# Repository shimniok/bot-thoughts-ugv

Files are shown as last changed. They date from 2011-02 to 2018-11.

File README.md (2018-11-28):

This is the repository of electronics and software for Data Bus and Troubled Child, my autonomous ground vehicles. 

* [Troubled Child](http://www.bot-thoughts.com/2014/06/avc-sharc-fsv.html) is a 1986 Jeep Grand Wagoneer that took 1st place in the 2014 Sparkfun AVC.
* [Data Bus](http://www.bot-thoughts.com/p/robot-mag-data-bus.html) is a 1:10 scale RC car that took 3rd place in the 2012 Sparkfun AVC.

The repository contains source code, schematics, board layouts, and documentation. Mostly this is a catch-all for what I worked on in 2010-2014.

* [Current Software](https://github.com/shimniok/diyrovers) - updated versions of the mbed software that handles pose estimation, navigation, and path following
* ```Software/``` - *older* mbed software that handles pose estimation, navigation, path following
* ```Documentation/``` - various supporting documents
* ```Hardware/``` - various hardware used in building and calibrating
* ```Electronics/``` - catch-all of circuit/layout designs varying from experiment to tried and tossed

Some of the electronics are now products on [Tindie.com](https://www.tindie.com/stores/bot_thoughts/) and they have their own repositories, shown below.

# Rover Products
* [RoverMux](https://github.com/shimniok/RoverMux) tried and true 3 channel R/C Multiplexer
* [RoverBaseboard](https://github.com/shimniok/RoverBaseboard) - a baseboard making it easy to hook up servos and sensors to an mbed/LPCXpresso
* [RoverGyro](https://github.com/shimniok/RoverGyro) - a breakout for low drift MAX21000 gyro (untested)
* [RoverPower](https://github.com/shimniok/RoverPower) - high current 5V power supply (untested)
* [RoverMeter](https://github.com/shimniok/RoverMeter) - I2C-based current monitor (untested)

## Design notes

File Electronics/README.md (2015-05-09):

# Circuits for Sparkfun AVC Robot 2011

Various circuits for 2011 AVC ground robot

* 5vadcmbed/ - 5V-capable ADC for mbed
* Block Diagram.sch - block diagram for data bus
* cmucambridge/ - serial to I2C bridge for CMUcam (incomplete)
* duplexoptoiso/ - full duplex opto isolator, used during GPS experiments
* gfxlcd/ - graphic LCD
* microsdbreakout/ - maybe an old version of [eeZeeMicroSD](https://github.com/shimniok/eeZeeMicroSD)
* motherboard/ - original verion(s) of [RoverBaseboard](https://github.com/shimniok/RoverBaseboard)
* pdmodule/ - simple power distribution module 
* powersupply/ - power supply for MCU
* powersupply5/ - power supply for MCU
* rangeri2c/ - early version of analog-to-I2C module?
* rckillswitch/ - early version of [RoverMux](https://github.com/shimniok/RoverMux)
* seriali2cbridge/ - serial to I2C bridge, probably for AVRcam
* venusgps/ - Venus GPS mounting board(?)
* warningflasher/ - a warning flasher letting people know the vehicle is in autonomous mode
* wheelencoderadapter/ - an early version of [RoverEncoder](https://github.com/shimniok/RoverEncoder)

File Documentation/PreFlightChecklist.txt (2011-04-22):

=====================================================
================ Pre-Event Checklist ================ 
=====================================================

[ ] Correct config used, waypoints, declination to SFE site
[ ] All stuff packed (see PitKit.txt checklist)
[ ] Tool kit inventory, load in vehicle

=====================================================
================ Pre-Flight Checklist =============== 
=====================================================

[ ] Wheels mounted tightly

[ ] Battery connected and charged

[ ] Start button plugged in

[ ] Obj detection plugged in

[ ] Compass connected

[ ] GPS connected

[ ] Body clips on

[ ] Obj detection mounted

[ ] Compass/GPS mounted, aligned

[ ] AHRS mounted and connected

[ ] SD Card installed

=====================================================
==================== Staging Area =================== 
=====================================================

[ ] Camera powered on

[ ] MCU powered on

[ ] Wheel encoders working, not skipping

[ ] Motor power connected

[ ] Remote control is OFF

[ ] ESC powered up, operational

[ ] AHRS functional

[ ] File logging functioning

[ ] GPS fix established

=====================================================
=============== Post-Fight Checklist ================ 
=====================================================

[ ] charge battery

[ ] remove data log and plot

[ ] download camera data

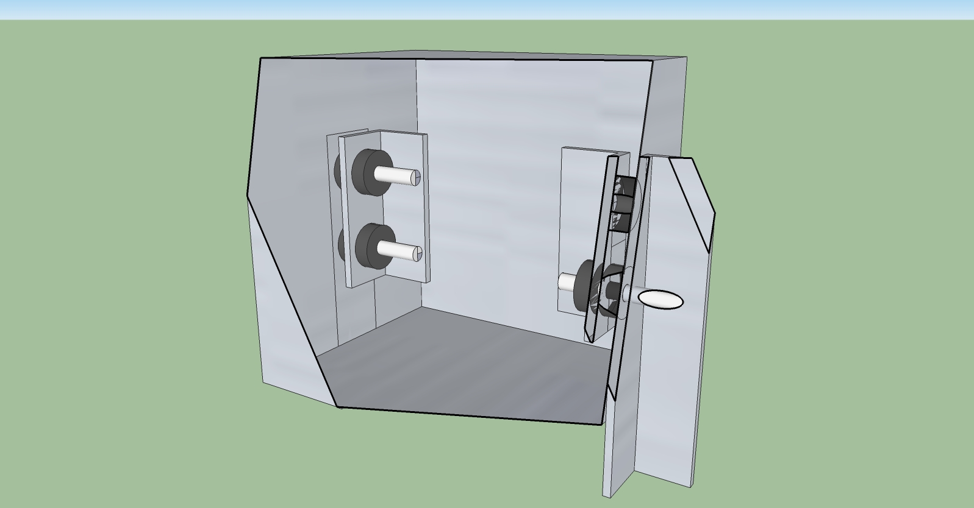
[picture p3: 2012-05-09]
Hardware/AVRcamMount.jpg

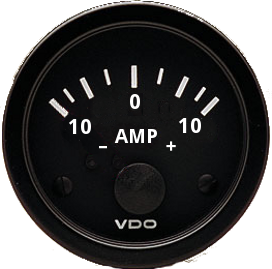
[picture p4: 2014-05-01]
Software/GCS/BotThoughtsGCS/src/com/botthoughts/gcs/resources/ammeter3.png

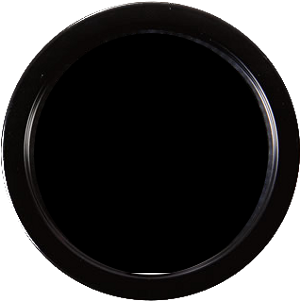
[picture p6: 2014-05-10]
Software/GCS/BotThoughtsGCS/src/com/botthoughts/gcs/resources/compass.png

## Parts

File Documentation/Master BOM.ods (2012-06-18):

Bot Thoughts UGV “Data Bus” for 2012 Sparkfun AVC |  |  |  |  | Key
As complete as I can make it; I'm sure I'm forgetting some things. |  |  |  |  | used it | didn't use it | inaccurate
Master BOM
Item | Description | Supplier | Manufacturer | Part Number | Cost | Qty | Total | Changes
RC Car Chassis
R/C Car | ElectrixRC Circuit 1/10 RC Stadium Truck | RC Hobbies | ElectrixRC | n/a | $140.00 | 1 | $140.00
Battery | 4000mAH 25C ROAR battery | Hobbypartz | Gens Ace | 98P-25C-2400-2S1P-HardCase | $20.00 | 1 | $20.00
Tires | Traxxas Anaconda on All Star black chrome (pair) | RC Hobbies | Traxxas | 3776A | $25.99 | 2 | $51.98
Springs | ElectrixRC Springs, Stiff | A Main Hobbies | ECX | ECX1080 | $6.39 | 1 | $6.39
Shock oil | Losi 50wt shock oil | Hobbytown USA | Losi | LOSA5227 | $4.00 | 1 | $4.00 | 2012
ESC | Hobbywing eZrun 35A ESC | Hobbypartz | HobbyWing | 07E-eZRun-35A-SL-ESC | $29.64 | 1 | $29.64 | 2012
Motor | Tacon 3000Kv 3660-540L-8T | Hobbypartz | Tacon | 96M213-3660-3000KV-8T | $32.20 | 1 | $32.20 | 2012
Body | Skool Bus lexan body | Tower Hobbies | Parma | LXEER5 | $23.99 | 1 | $23.99
Paint | RC Body paint (3 colors) | RC Hobbies | Pactra / Testors | various | $6.29 | 3 | $18.87
Body clips | RC 1:10 body clips | A Main Hobbies | ECX | ECX1048 | $1.89 | 1 | $1.89
Body posts | 2 pair, HPI body posts | RC Hobbies | HPI | #6507 | $5.59 | 2 | $11.18
Lexan sheet | Lexan sheet, .093”x8”x10” electronics platform, bumper | Home Depot | SABIC Innovative Plastics | n/a | $3.98 | 1 | $3.98 | 2012
Brass strip | Brass strip, 2” x 12” x 0.032” | Big Tool Box | K&S | n/a | $3.79 | 1 | $3.79
Brass strip | Brass strip, 1” x 12” x 0.032” | Big Tool Box | K&S | n/a | $2.29 | 1 | $2.29
Aluminum strip | Front skid plate/bumper mount | Big Tool Box |  |  |  | 1 | $0.00 | 2012
Sheet aluminum | Front skid plate/bumper mount | Big Tool Box |  |  |  | 1 | $0.00 | 2012
Aluminum L | Cow catcher / bumper | Big Tool Box |  |  |  | 1 | $0.00 | 2012
Aluminum L | Electronics platform mounting | Big Tool Box |  |  |  | 1 | $0.00 | 2012
Aluminum L | Electronics platform mounting | Big Tool Box |  |  |  | 1 | $0.00 | 2012
Nylon PCB spacers | Spacers for Lexan platform, 0.375”, chassis front | All Electronics | unknown | SP-228 | $0.05 | 2 | $0.10
Aluminum rivets | Rivets for mounting brackets | self | parts bin | n/a | $0.00 | 2 | $0.00 | 2012
#10 Nylon Spacers | Spacers for motherboard mounting | self | parts bin | n/a | $0.00 | 4 | $0.00 | 2012
#10 nylock nuts | Nuts for electronics platform | self | parts bin | n/a | $0.00 | 4 | $0.00 | 2012
#10 x 1.5” machine screw | Bolts for electronics platform | self | parts bin | n/a | $0.00 | 4 | $0.00 | 2012
Deans connectors | Deans battery connectors | A Main Hobbies | Deans | WSD1300 | $2.99 | 2 | $5.98 | 2012
Microcontroller and Motherboard
Microcontroller | NXP mbed LPC1768 ARM Cortex M3 microcontroller | Sparkfun | NXP | DEV-09564 | $59.95 | 1 | $59.95
microSD socket | microSD slot | Sparkfun | Amphenol | PRT-00127 | $3.95 | 1 | $3.95 | 2012
microSD card | microSD card, 2G | Microcenter | unknown | unknown | $12.99 | 1 | $12.99 | 2012
LCD Display | Serial Graphic LCD | Sparkfun | Sparkfun | LCD-09351 | $34.95 | 1 | $34.95 | 2012
Interface buttons | SPST Normally Open Pushbutton Momentary Switch | Radio Shack | Radio Shack | 275-646, 275-644 | $2.99 | 3 | $8.97 | 2012
Sensors
GPS | Venus638FLPX SMA breakout board | Sparkfun | SkyTraq | GPS-11058 | $49.95 | 1 | $49.95 | 2012
GPS Ground plane | Tin sheet | Big Tool Box | K&S |  |  |  | $0.00 | 2012
IR Rangers | Sharp GP2Y0A02YK0F 150cm IR Ranger | Sparkfun | Sharp | SEN-08958 | $14.95 | 1 | $14.95 | 2012
IMU | Pololu MinIMU-9 | Pololu | Pololu | #1265 | $49.95 | 1 | $49.95 | 2012
Encoder sensors | QRE1113 analog breakout board | Sparkfun | Sparkfun | ROB-09453 | $2.95 | 1 | $2.95 | 2012
Encoder boards | Schmitt-trigger comparator interface board | Bot Thoughts | Bot Thoughts | n/a | $6.00 | 1 | $6.00 | 2012
RC Switch Board
74HC244 | Bus Driver / Switch | Newark | STMicro | 18C7559 | $0.57 | 1 | $0.57
LM258 | Operational Amplifier | Newark | STMicro | 89K0661 | $0.23 | 1 | $0.23
Power supply
LDO Regulator | 3A switching step-down regulator | Pololu | Pololu | D15V35F5S3 | $14.95 | 1 | $14.95
Misc Electronic Components
PCB | Printed circuit board, 1oz copper, 6” square | Digikey | MG Chemicals | 473-1006-ND | $7.24 | 1 | $7.24 | 2012
#2 nuts | Nuts for custom PCB mounting | Radio Shack |  |  | $1.99 | 1 | $1.99 | 2012
#2 standoffs | PCB standoffs | unknown | unknown |  | $0.00 | 0 | $0.00 | 2012
#2 bolts | Bolts for custom PCB mounting | Radio Shack |  |  | $1.99 | 1 | $1.99 | 2012
#4 nuts | Nuts for custom PCB mounting | Radio Shack |  |  | $1.99 | 1 | $1.99 | 2012
#4 standoffs | PCB standoffs, 100pk | Smallparts.com | unknown |  | $6.56 | 0.16 | $1.05 | 2012
#f bolts | Bolts for custom PCB mounting | Radio Shack |  |  | $1.99 | 1 | $1.99 | 2012
double sided tape | Double sided tape for sensor mounting | Hobby Lobby | Scotch 3M |  | $4.55 | 1 | $4.55 | 2012
 |  |  |  |  |  |  | $637.44 | TOTAL

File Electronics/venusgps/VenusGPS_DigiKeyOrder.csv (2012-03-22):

Digi-Key Part Number | Manufacturer Name | Manufacturer Part Number | Customer Reference | Quantity 1 | Quantity 2 | Quantity 3
3000K-ND | Keystone | 3000 | ? | 1 | ? | ?

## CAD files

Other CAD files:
Hardware/AVRcamMount.skp
Hardware/turntable.skp
Hardware/turntable_exploded.skp

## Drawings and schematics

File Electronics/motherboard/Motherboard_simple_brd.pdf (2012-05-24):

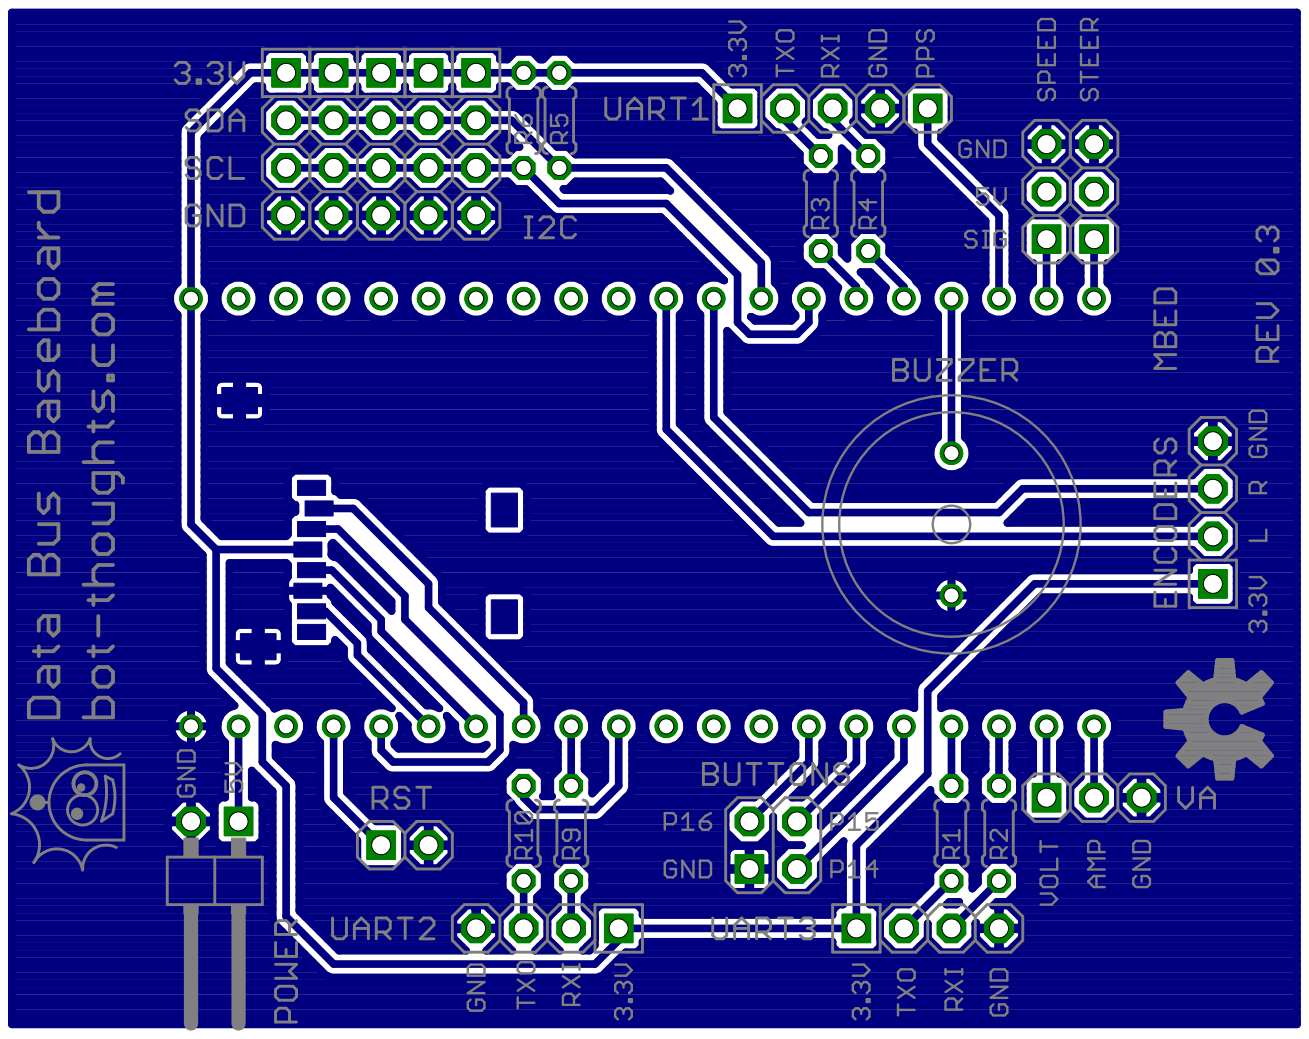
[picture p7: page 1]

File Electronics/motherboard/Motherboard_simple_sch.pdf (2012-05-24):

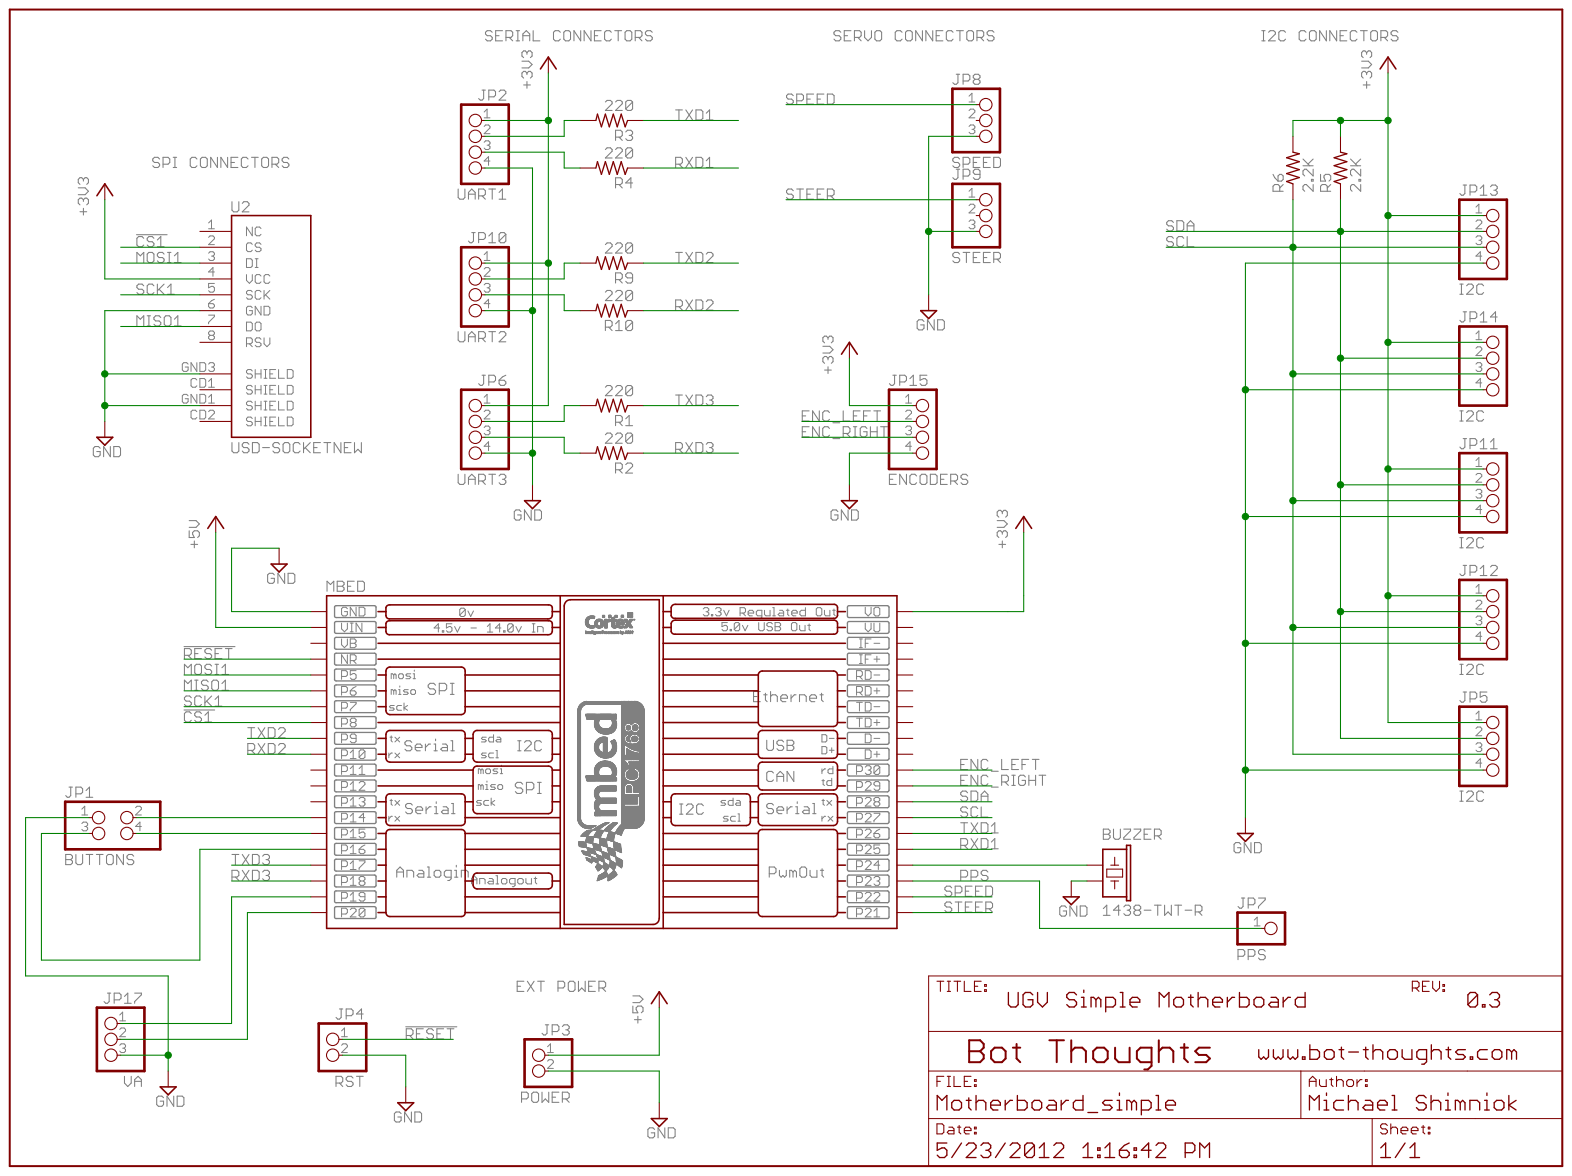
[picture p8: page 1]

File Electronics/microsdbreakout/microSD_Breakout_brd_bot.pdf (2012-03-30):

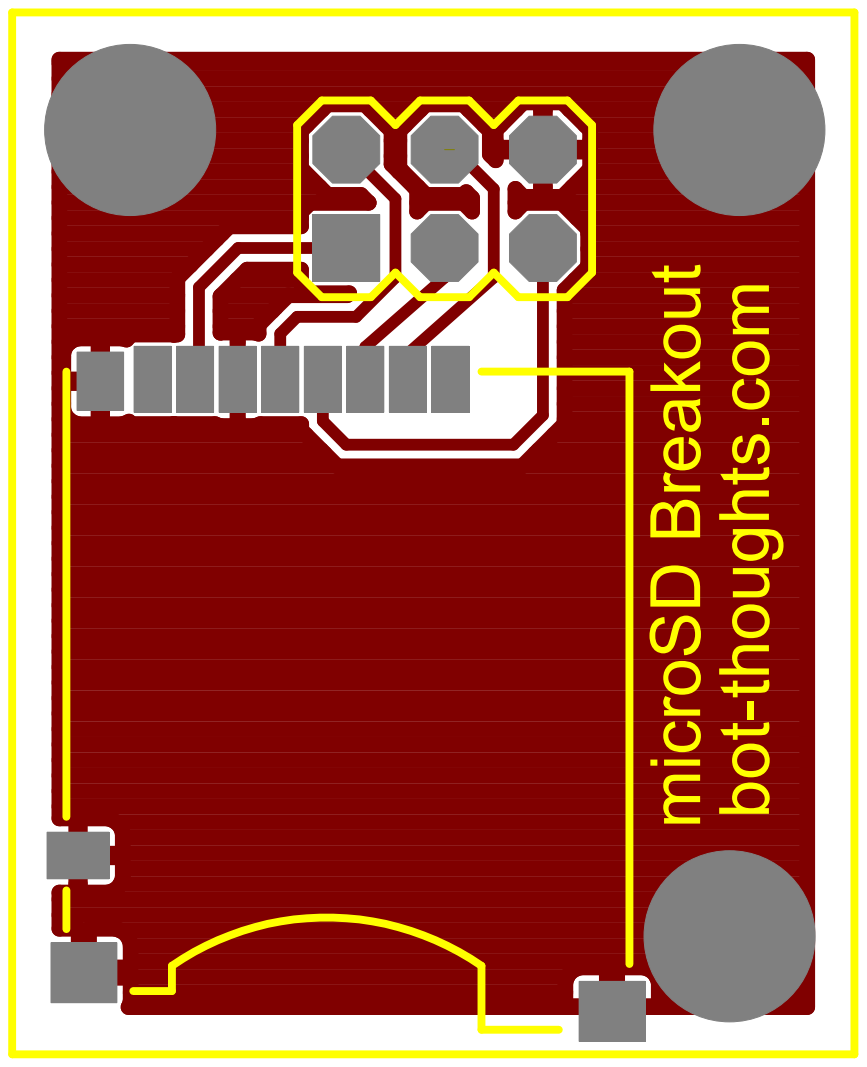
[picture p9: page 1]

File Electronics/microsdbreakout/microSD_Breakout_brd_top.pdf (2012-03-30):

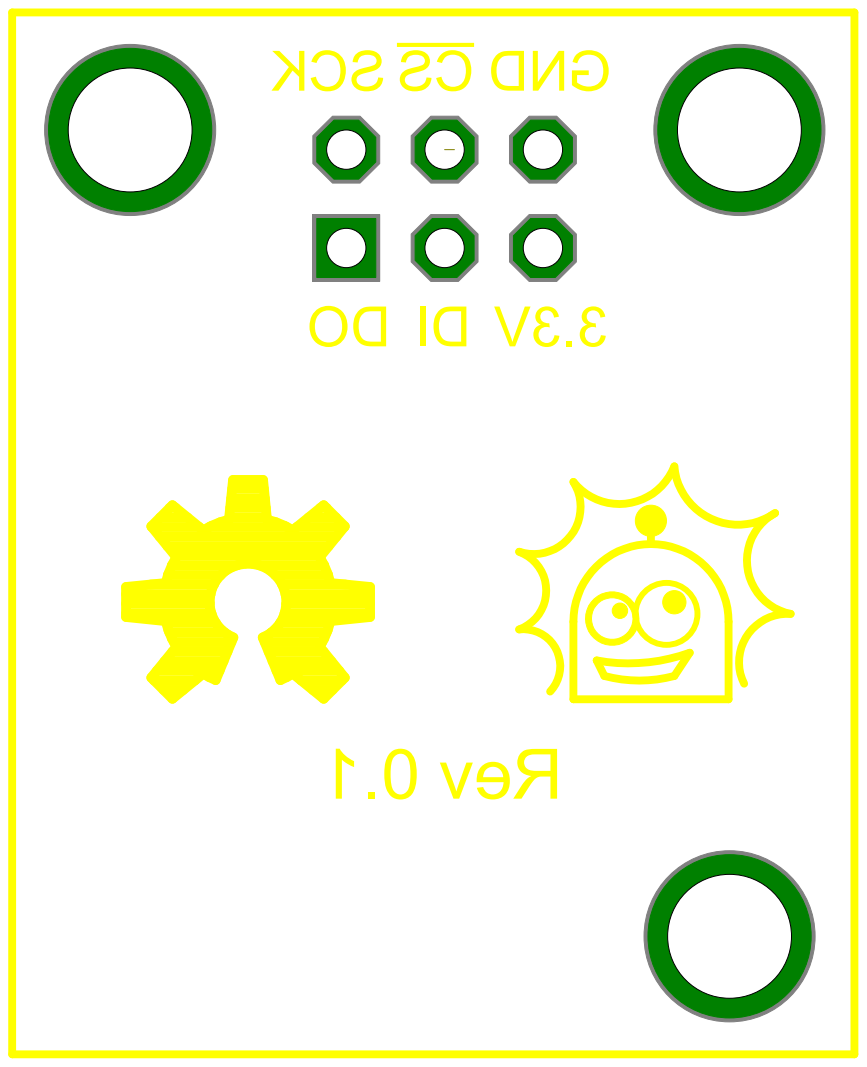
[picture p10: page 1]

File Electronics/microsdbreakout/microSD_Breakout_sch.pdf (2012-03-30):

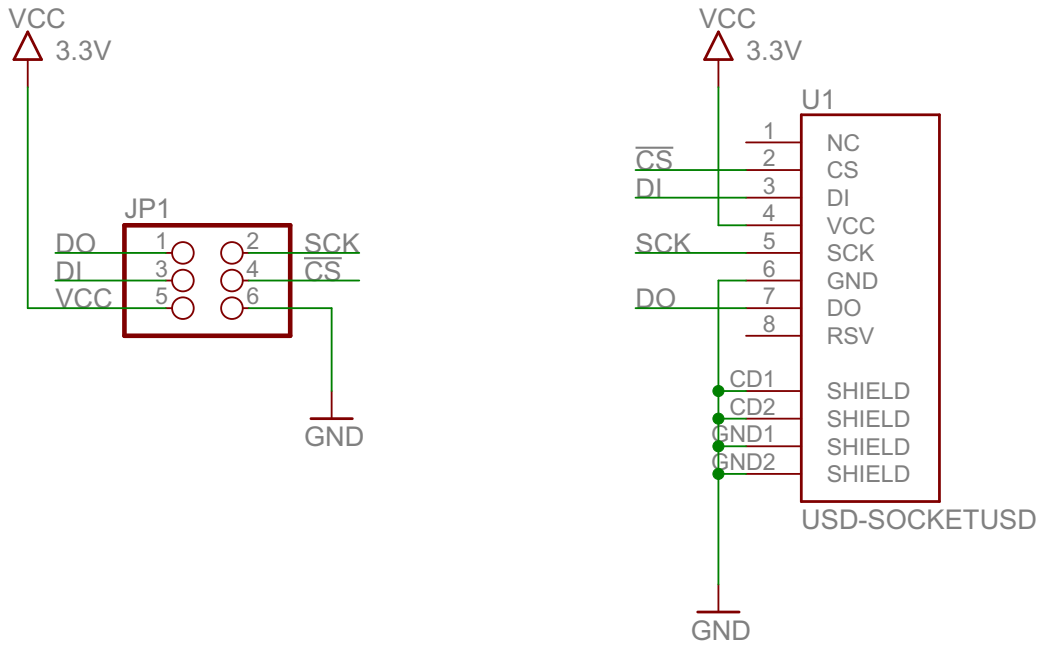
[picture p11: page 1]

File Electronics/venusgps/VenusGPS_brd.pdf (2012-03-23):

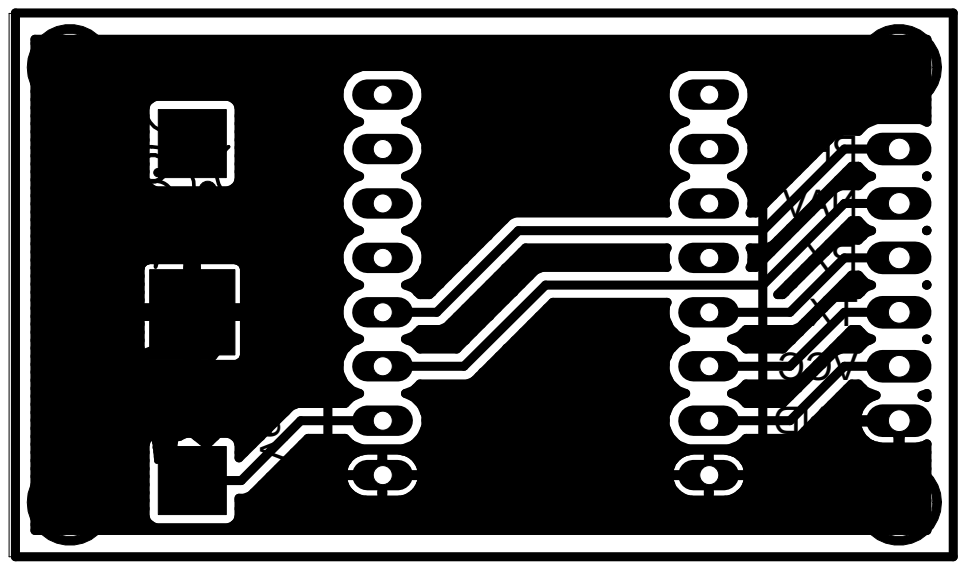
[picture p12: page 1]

bot-thoughts.com XT CCV DNGXR SPP VAN Venus GPS Interface 1. 0 veR

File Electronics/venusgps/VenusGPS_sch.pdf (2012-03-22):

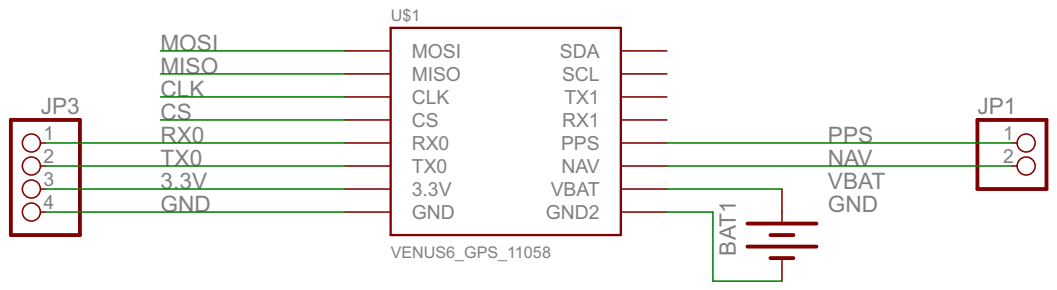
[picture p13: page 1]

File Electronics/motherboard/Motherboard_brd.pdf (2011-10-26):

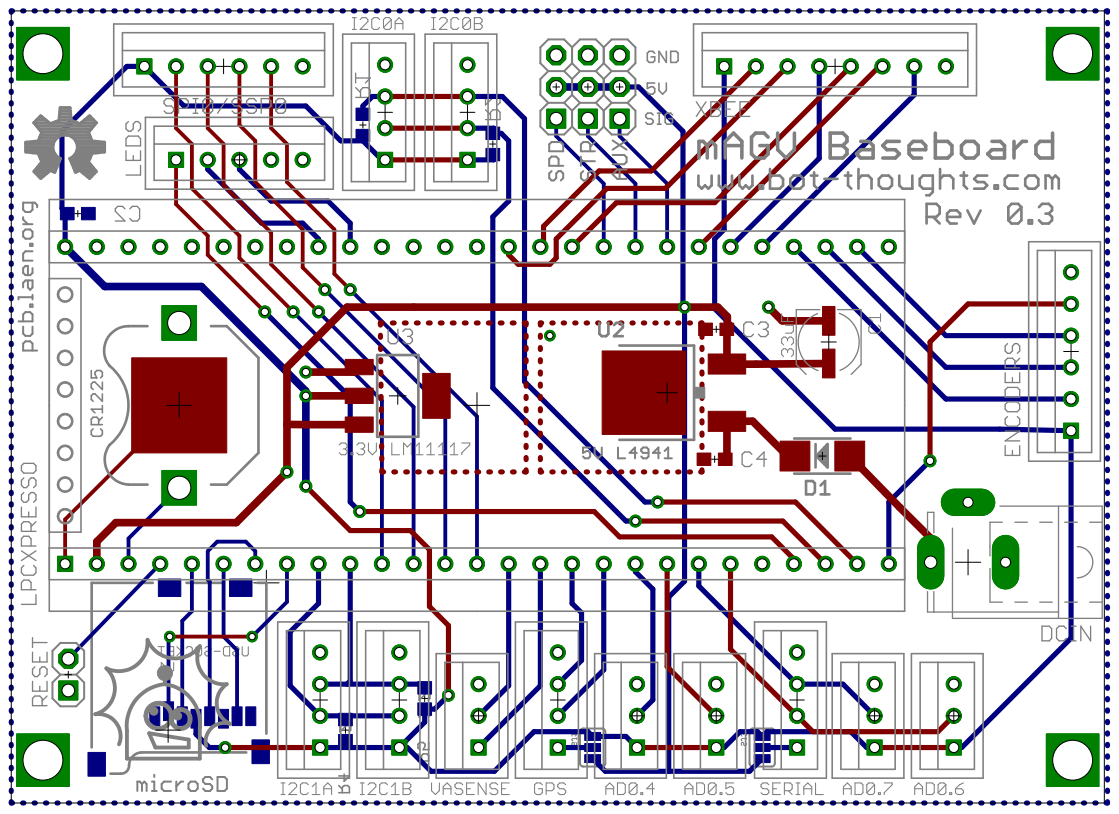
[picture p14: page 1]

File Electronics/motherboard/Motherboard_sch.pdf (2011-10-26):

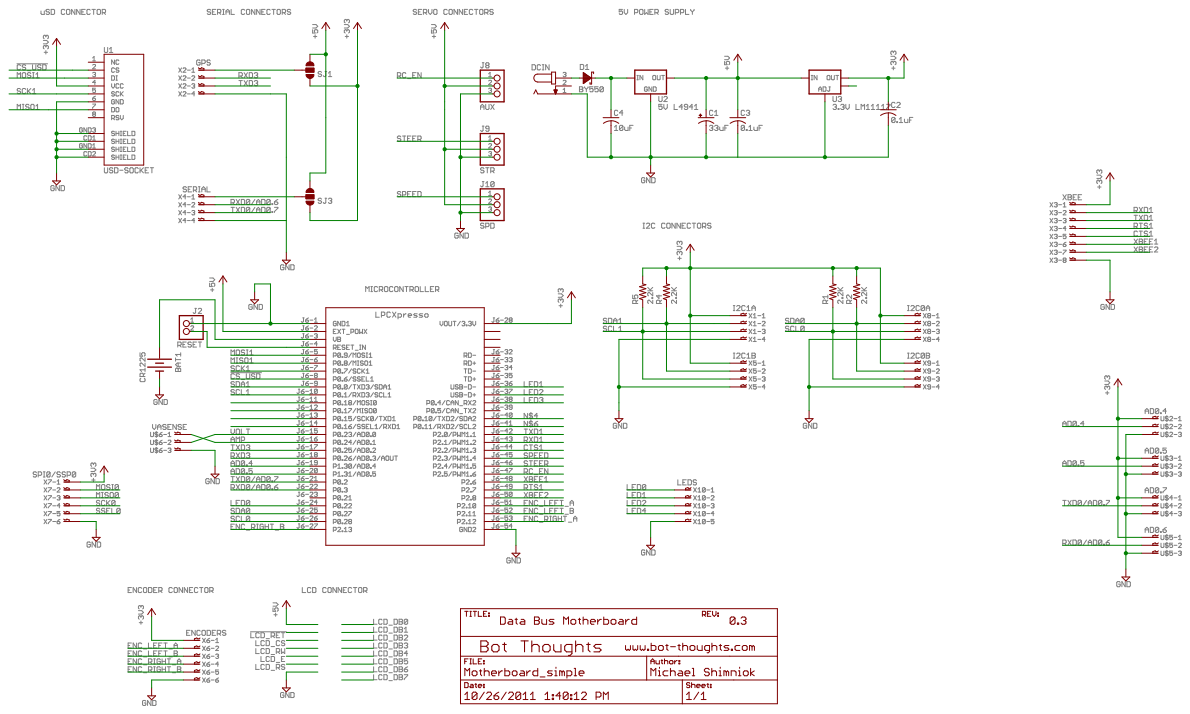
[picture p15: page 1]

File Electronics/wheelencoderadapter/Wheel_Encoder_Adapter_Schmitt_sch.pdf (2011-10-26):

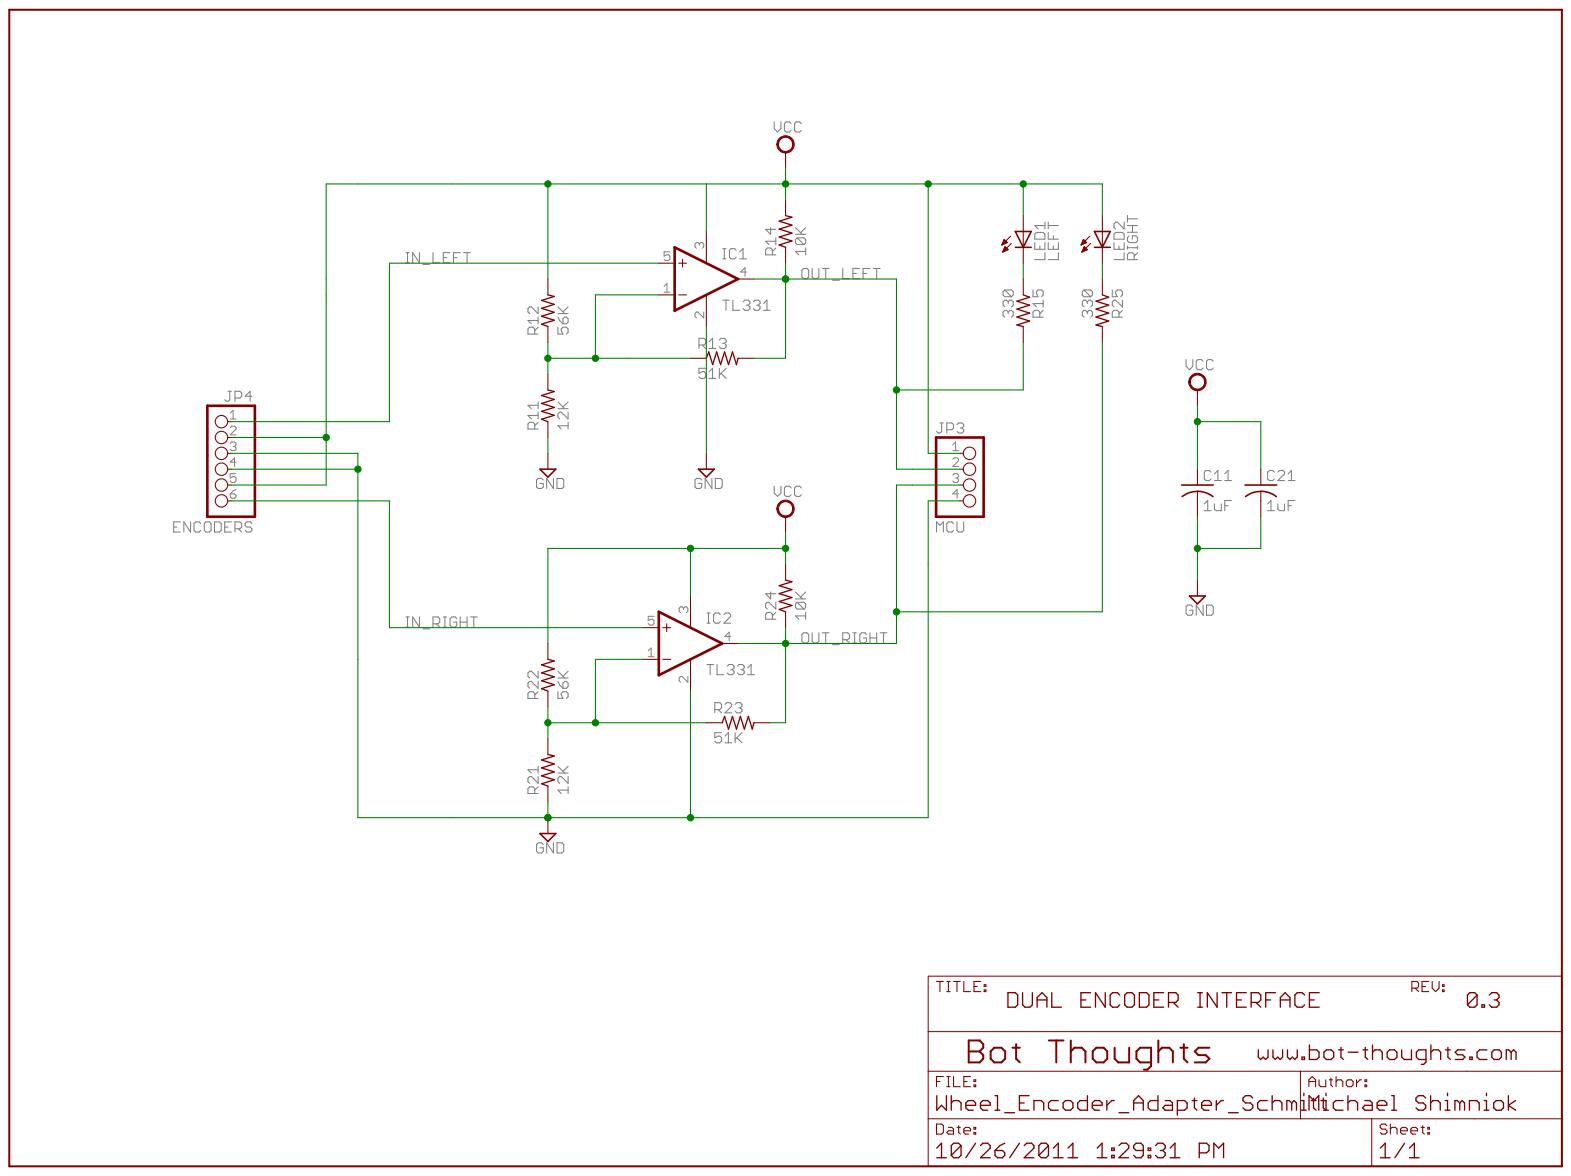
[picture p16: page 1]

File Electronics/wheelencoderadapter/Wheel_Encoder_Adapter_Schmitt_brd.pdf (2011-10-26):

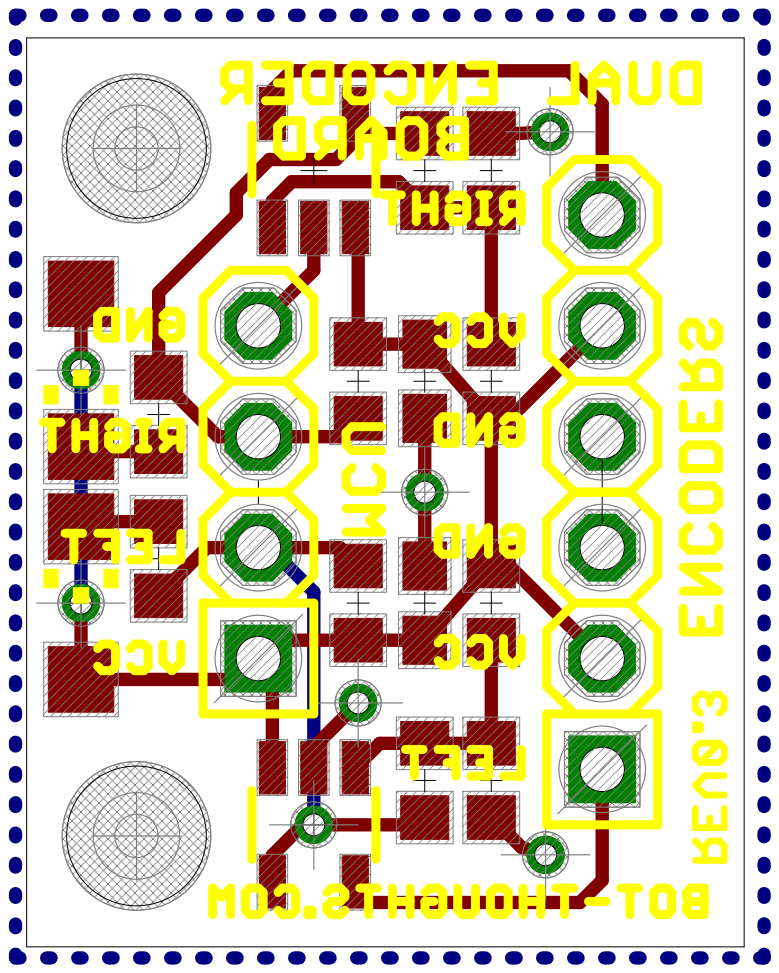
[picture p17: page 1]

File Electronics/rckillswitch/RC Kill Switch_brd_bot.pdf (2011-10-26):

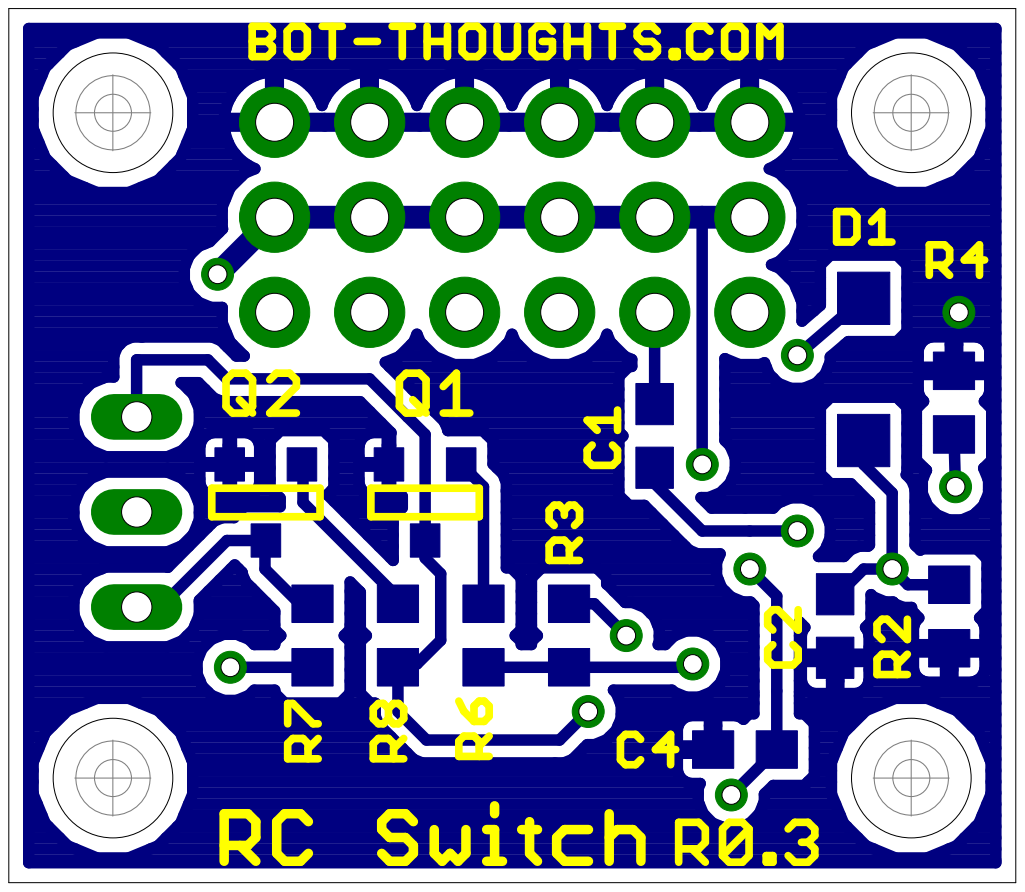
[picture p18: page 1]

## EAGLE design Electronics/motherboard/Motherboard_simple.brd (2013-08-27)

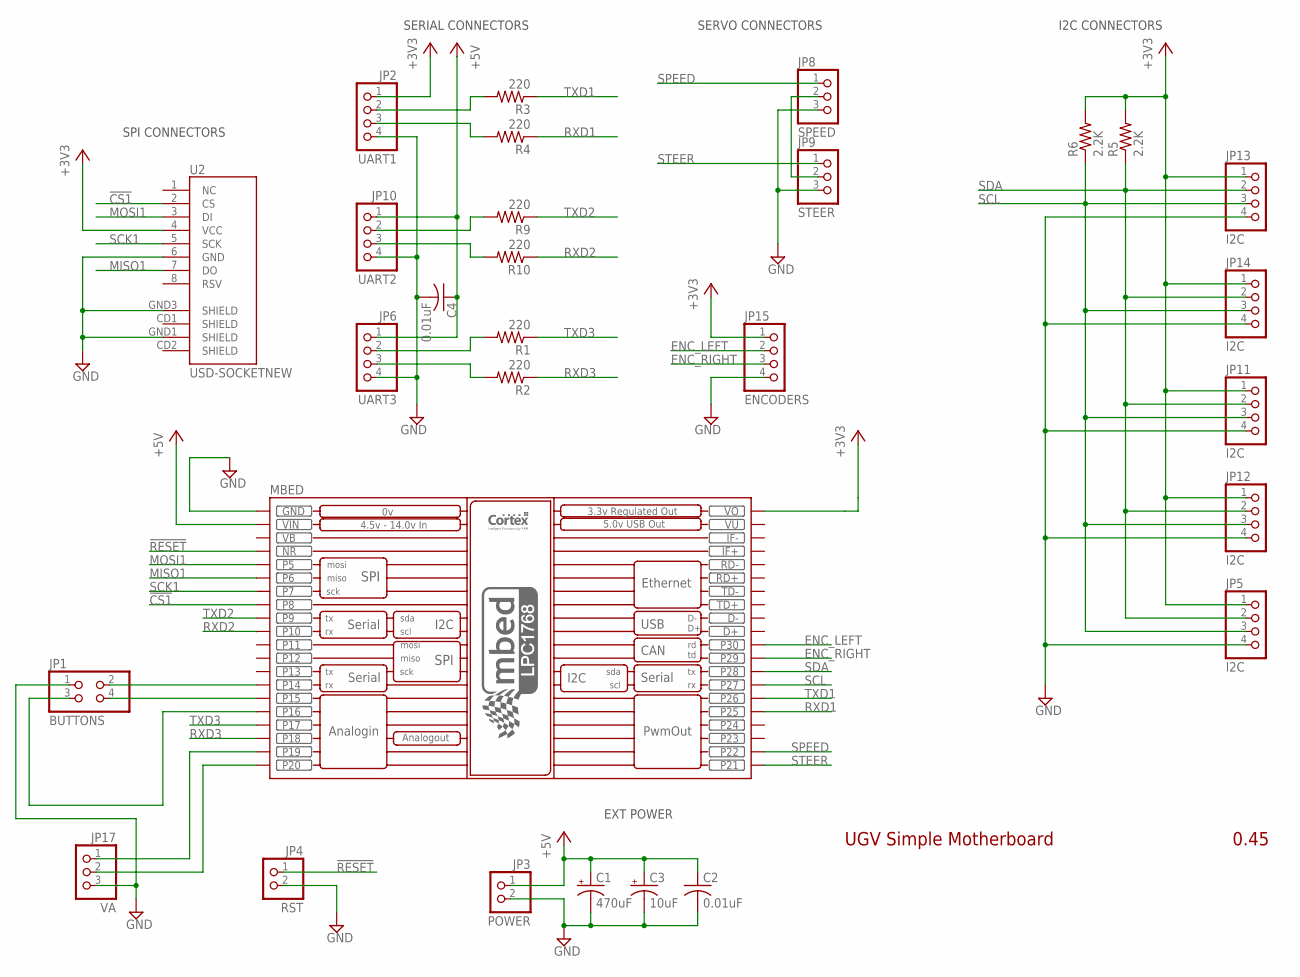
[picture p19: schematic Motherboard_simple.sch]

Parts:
C1: 470uF; E2,5-6
C2, C4: 0.01uF; C050-025X075
C3: 10uF; E2,5-6
JP1: BUTTONS; 2X02
JP2: UART1; 1X04-S
JP3: POWER; 1X02-S
JP4: RST; 1X02-S
JP5, JP11, JP12, JP13, JP14: I2C; 1X04-S
JP6: UART3; 1X04-S
JP8: SPEED; 1X03-S
JP9: STEER; 1X03-S
JP10: UART2; 1X04-S
JP15: ENCODERS; 1X04-S
JP17: VA; 1X03-S
MBED: MBED_NXP_LPC1768; MBED-KIT; MPN 2212S-20SG-85
R1, R2, R3, R4, R9, R10: 220; 0204/5; MPN WCR0805-220RFI
R5, R6: 2.2K; 0204/5
U2: USD-SOCKETNEW; MICRO-SD-SOCKET-PP

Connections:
!CS1: MBED.P$8 (P8), U2.2 (CS)
!RESET: JP4.1, MBED.NR
+3V3: JP2.1, JP5.1, JP11.1, JP12.1, JP13.1, JP14.1, JP15.1, MBED.VOUT (VO), R5.2, R6.2, U2.4 (VCC)
+5V: C1.+, C2.1, C3.+, C4.1, JP3.1, JP6.1, JP10.1, MBED.VIN
AMP: JP17.2, MBED.P$20 (P20)
ENC_LEFT: JP15.2, MBED.P$30 (P30)
ENC_RIGHT: JP15.3, MBED.P$29 (P29)
GND: C1.-, C2.2, C3.-, C4.2, JP1.1, JP2.4, JP3.2, JP4.2, JP5.4, JP6.4, JP8.3, JP9.3, JP10.4, JP11.4, JP12.4, JP13.4, JP14.4, JP15.4, JP17.3, MBED.GND, U2.6 (GND), U2.GND1 (SHIELD), U2.GND3 (SHIELD)
MISO1: MBED.P$6 (P6), U2.7 (DO)
MOSI1: MBED.P$5 (P5), U2.3 (DI)
unnamed: JP6.2, R1.2
unnamed: JP6.3, R2.2
unnamed: JP8.2, JP9.2
unnamed: JP1.2, MBED.P$14 (P14)
unnamed: JP17.1, MBED.P$19 (P19)
unnamed: JP1.4, MBED.P$15 (P15)
unnamed: JP1.3, MBED.P$16 (P16)
unnamed: JP2.2, R3.2
unnamed: JP2.3, R4.2
unnamed: JP10.2, R9.2
unnamed: JP10.3, R10.2
RXD1: MBED.P$25 (P25), R4.1
RXD2: MBED.P$10 (P10), R10.1
RXD3: MBED.P$18 (P18), R2.1
SCK1: MBED.P$7 (P7), U2.5 (SCK)
SCL: JP5.3, JP11.3, JP12.3, JP13.3, JP14.3, MBED.P$27 (P27), R6.1
SDA: JP5.2, JP11.2, JP12.2, JP13.2, JP14.2, MBED.P$28 (P28), R5.1
SPEED: JP8.1, MBED.P$22 (P22)
STEER: JP9.1, MBED.P$21 (P21)
TXD1: MBED.P$26 (P26), R3.1
TXD2: MBED.P$9 (P9), R9.1
TXD3: MBED.P$17 (P17), R1.1
VB: MBED.VB
VU: MBED.VU

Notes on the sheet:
SERVO CONNECTORS
SPI CONNECTORS
I2C CONNECTORS
SERIAL CONNECTORS
UGV Simple Motherboard
0.45
EXT POWER

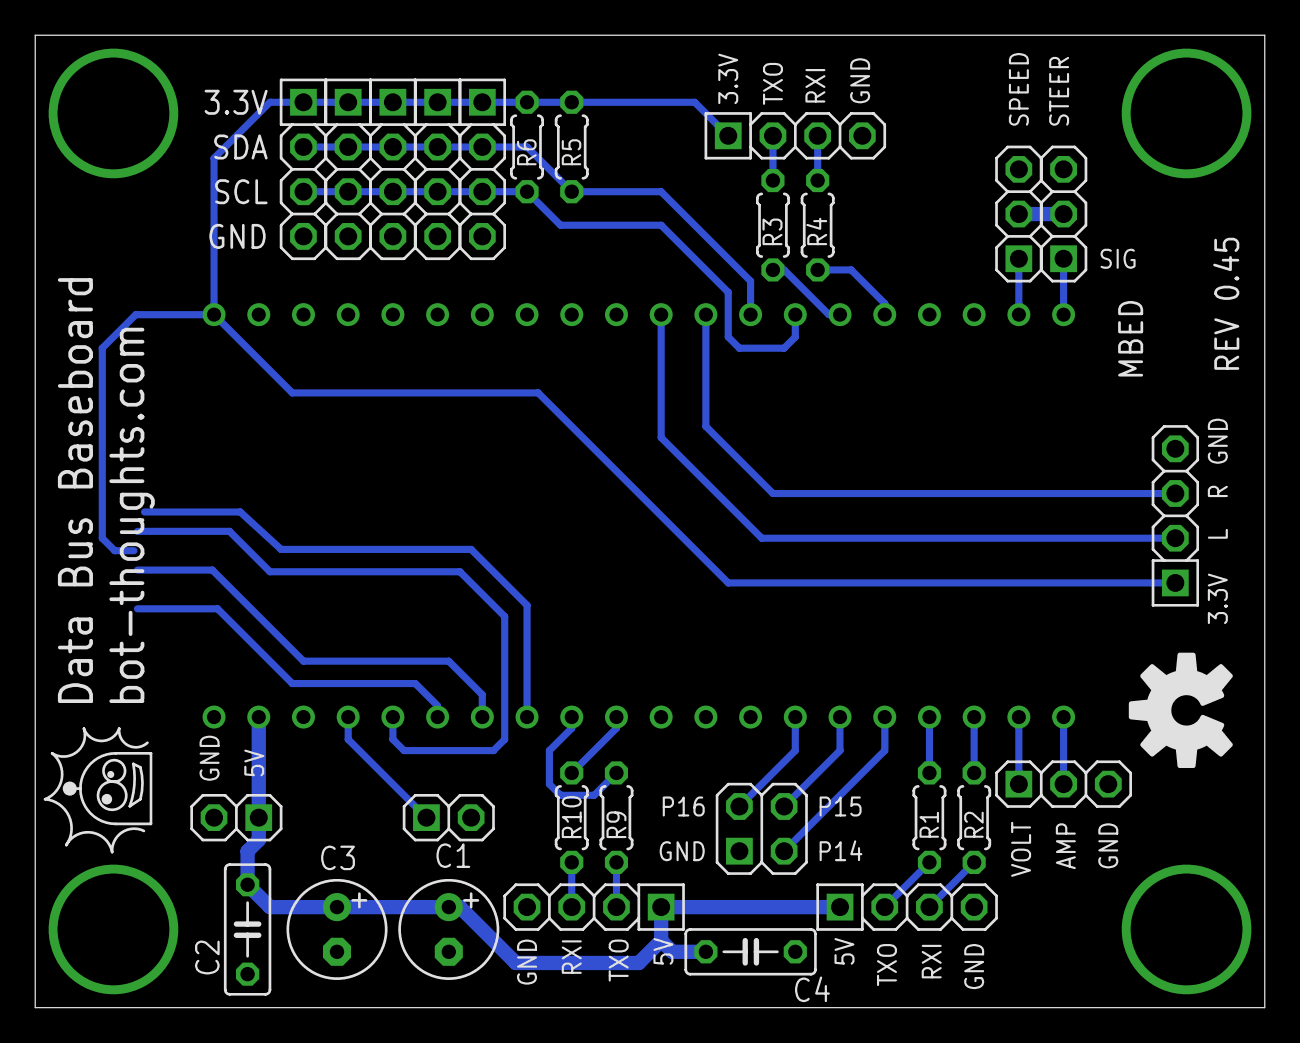
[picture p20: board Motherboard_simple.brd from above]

Board: 2 copper layers, 69.8 x 55.2 mm, 29 parts (1 on the bottom side), 32 nets.

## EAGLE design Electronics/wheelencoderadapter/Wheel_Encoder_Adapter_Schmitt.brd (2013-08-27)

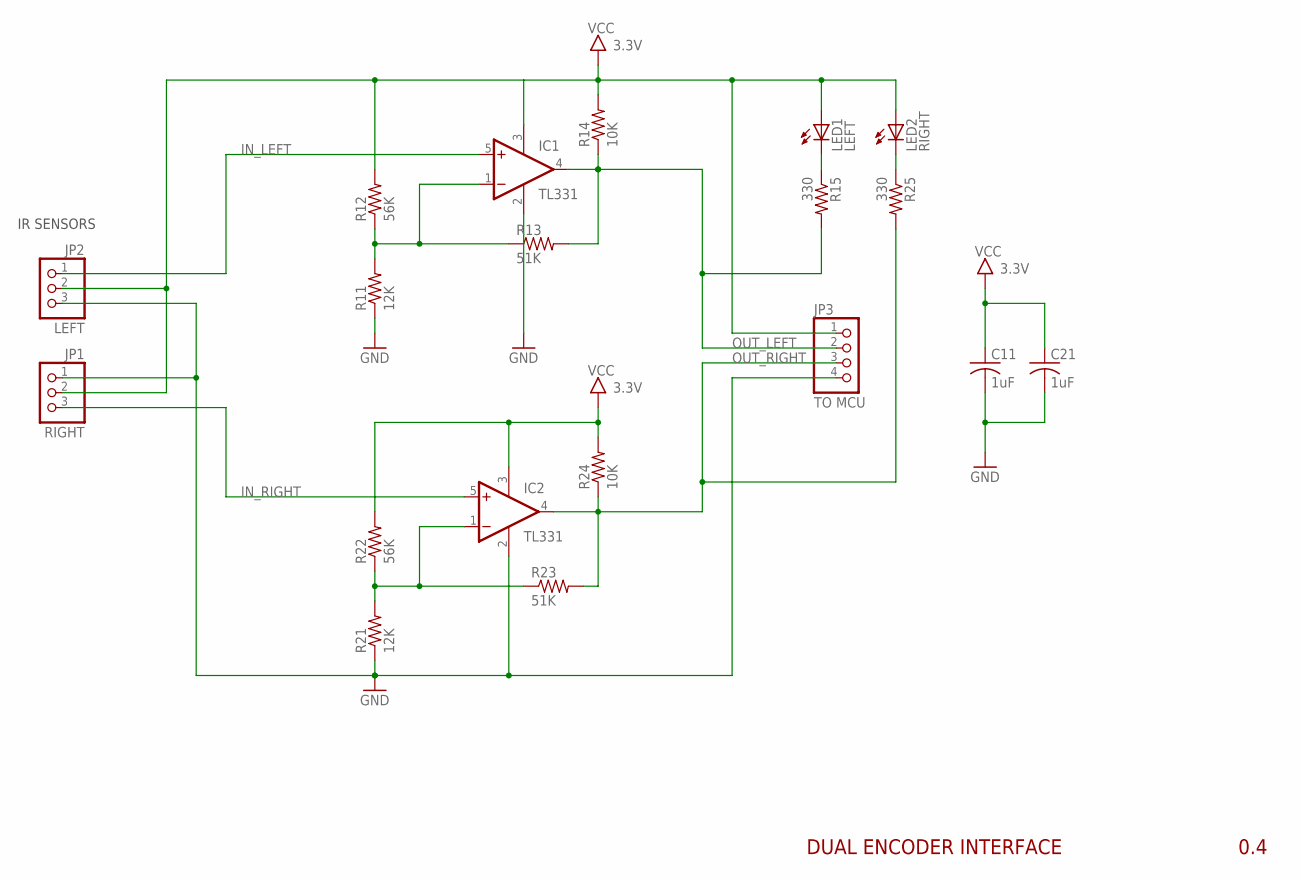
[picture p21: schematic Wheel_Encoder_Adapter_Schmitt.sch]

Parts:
C11, C21: 1uF; C0603; PARTNO C1608X7R1A105M
IC1, IC2: TL331; DBV-R-PDSO-G5; PARTNO TL331IDBVR
JP1: RIGHT; 1X03-S
JP2: LEFT; 1X03-S
JP3: TO MCU; 1X04-S
LED1: LEFT; CHIPLED_1206; PARTNO LG N971-KN-1
LED2: RIGHT; CHIPLED_1206; PARTNO LG N971-KN-1
R11, R21: 12K; R0603; PARTNO ERJ-3EKF1202V
R12, R22: 56K; R0603; PARTNO ERJ-3EKF5602V
R13, R23: 51K; R0603; PARTNO ERJ-3EKF5102V
R14, R24: 10K; R0603; PARTNO ERJ-3GEYJ103V
R15, R25: 330; R0603; PARTNO ERJ-3GEYJ331V

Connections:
GND: C11.2, C21.2, IC1.2 (GND), IC2.2 (GND), JP1.1, JP2.3, JP3.4, R11.1, R21.1
IN_LEFT: IC1.5 (+IN), JP2.1
IN_RIGHT: IC2.5 (+IN), JP1.3
unnamed: LED1.C, R15.1
unnamed: IC1.1 (-IN), R11.2, R12.1, R13.1
unnamed: LED2.C, R25.1
unnamed: IC2.1 (-IN), R21.2, R22.1, R23.1
OUT_LEFT: IC1.4 (OUT), JP3.2, R13.2, R14.1, R15.2
OUT_RIGHT: IC2.4 (OUT), JP3.3, R23.2, R24.1, R25.2
VCC: C11.1, C21.1, IC1.3 (V+), IC2.3 (V+), JP1.2, JP2.2, JP3.1, LED1.A, LED2.A, R12.2, R14.2, R22.2, R24.2

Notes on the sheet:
DUAL ENCODER INTERFACE
0.4
IR SENSORS

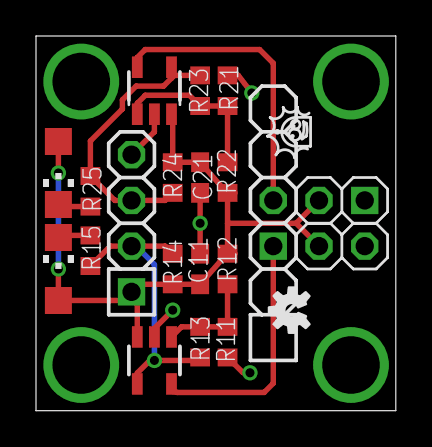
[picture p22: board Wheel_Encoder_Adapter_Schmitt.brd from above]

Board: 2 copper layers, 20.0 x 20.8 mm, 19 parts (0 on the bottom side), 10 nets.

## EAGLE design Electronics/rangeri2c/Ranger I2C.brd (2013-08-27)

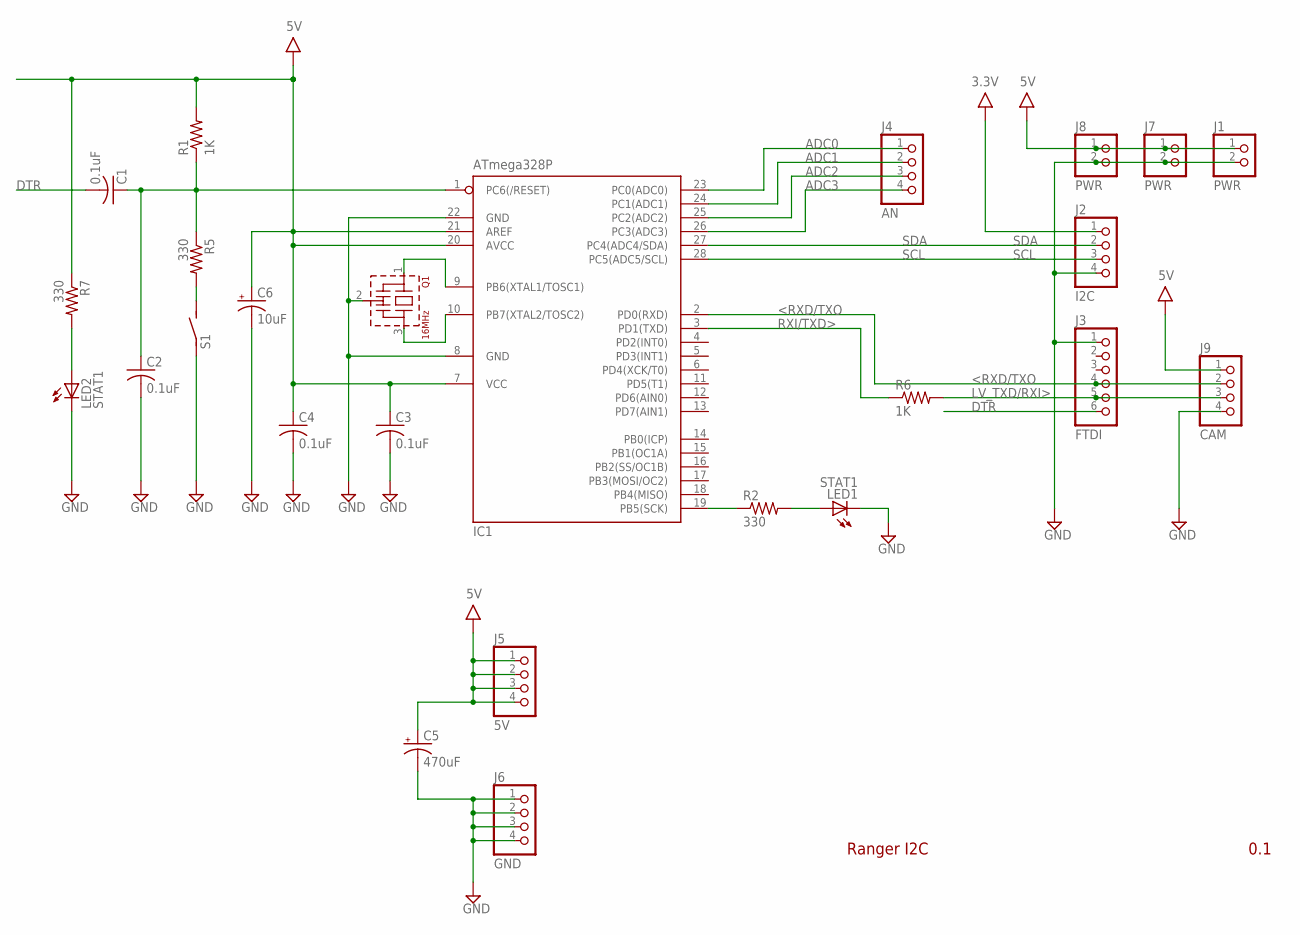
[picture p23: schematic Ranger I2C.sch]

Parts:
C1: 0.1uF; C050-024X044; PARTNO CC0603ZRY5V7BB104
C2, C3, C4: 0.1uF; C050-024X044; PARTNO C1608X5R0J105K
C5: 470uF; E2,5-6
C6: 10uF; E2,5-6
IC1: ATmega328P; DIL28-3; PARTNO DEV-10524
J1, J7, J8: PWR; 1X02-S
J2: I2C; 1X04-S; PARTNO 2211S-04G
J3: FTDI; 1X06-S; PARTNO 2211S-06G
J4: AN; 1X04-S; PARTNO 2211S-04G
J5: 5V; 1X04-S; PARTNO 2211S-04G
J6: GND; 1X04-S; PARTNO 2211S-04G
J9: CAM; 1X04-S; PARTNO 2211S-04G
LED1, LED2: STAT1; LED3MM
Q1: 16MHz; CSTLS_G9; PARTNO AWCR-16.00MD
R1: 1K; 0204/5
R2, R5, R7: 330; 0204/5; PARTNO CRCW0603330RJNEA
R6: 1K; 0204/5; PARTNO CRCW0603330RJNEA
S1: RESET\; EVQ11X09; PARTNO SALVAGE

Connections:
3.3V: J2.1
5V: C3.1, C4.1, C5.+, C6.+, IC1.7 (VCC), IC1.20 (AVCC), IC1.21 (AREF), J1.1, J5.1, J5.2, J5.3, J5.4, J7.1, J8.1, J9.1, R1.2, R7.1
<RXD/TXO: IC1.2 (PD0(RXD)), J3.4, J9.2
ADC0: IC1.23 (PC0(ADC0)), J4.1
ADC1: IC1.24 (PC1(ADC1)), J4.2
ADC2: IC1.25 (PC2(ADC2)), J4.3
ADC3: IC1.26 (PC3(ADC3)), J4.4
DTR: C1.2, J3.6
GND: C2.2, C3.2, C4.2, C5.-, C6.-, IC1.8 (GND), IC1.22 (GND), J1.2, J2.4, J3.1, J6.1, J6.2, J6.3, J6.4, J7.2, J8.2, J9.4, LED1.K (C), LED2.K (C), Q1.2 (VSS), S1.1
LV_TXD/RXI>: J3.5, J9.3, R6.2
unnamed: IC1.9 (PB6(XTAL1/TOSC1)), Q1.1
unnamed: IC1.10 (PB7(XTAL2/TOSC2)), Q1.3
unnamed: LED1.A, R2.2
unnamed: IC1.19 (PB5(SCK)), R2.1
unnamed: C1.1, C2.1, IC1.1 (PC6(/RESET)), R1.1, R5.1
unnamed: R5.2, S1.2
unnamed: LED2.A, R7.2
RXI/TXD>: IC1.3 (PD1(TXD)), R6.1
SCL: IC1.28 (PC5(ADC5/SCL)), J2.3
SDA: IC1.27 (PC4(ADC4/SDA)), J2.2

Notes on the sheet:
Ranger I2C
0.1

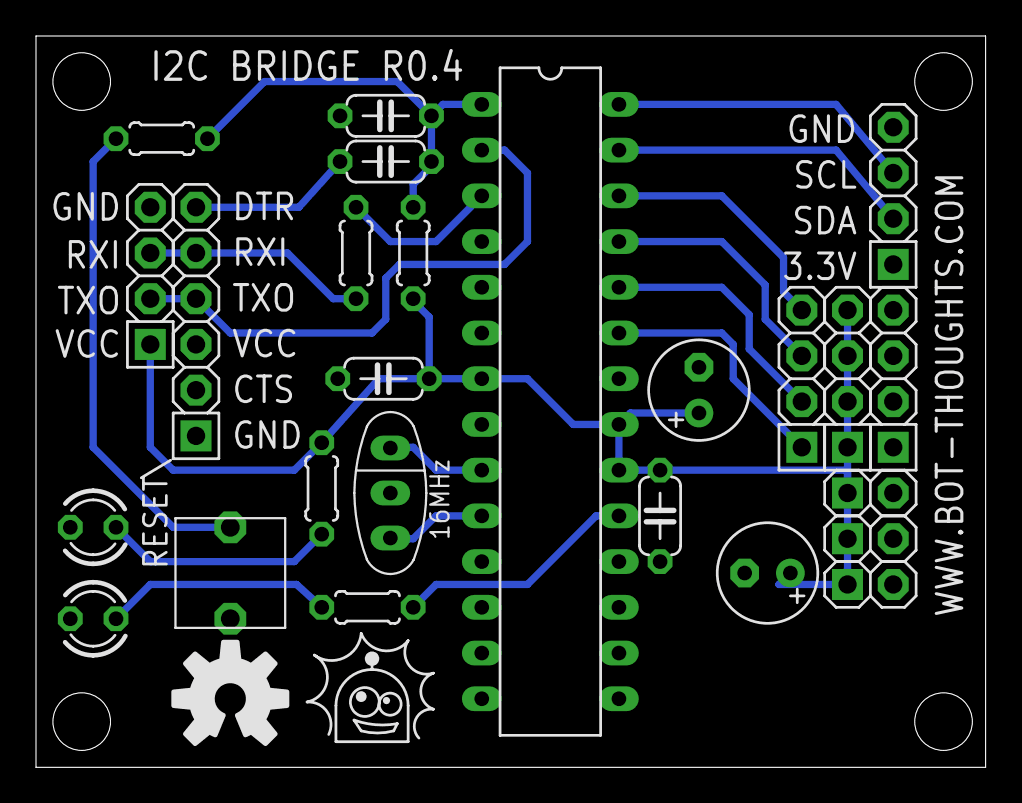
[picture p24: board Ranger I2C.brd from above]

Board: 2 copper layers, 52.8 x 40.6 mm, 25 parts (0 on the bottom side), 19 nets.

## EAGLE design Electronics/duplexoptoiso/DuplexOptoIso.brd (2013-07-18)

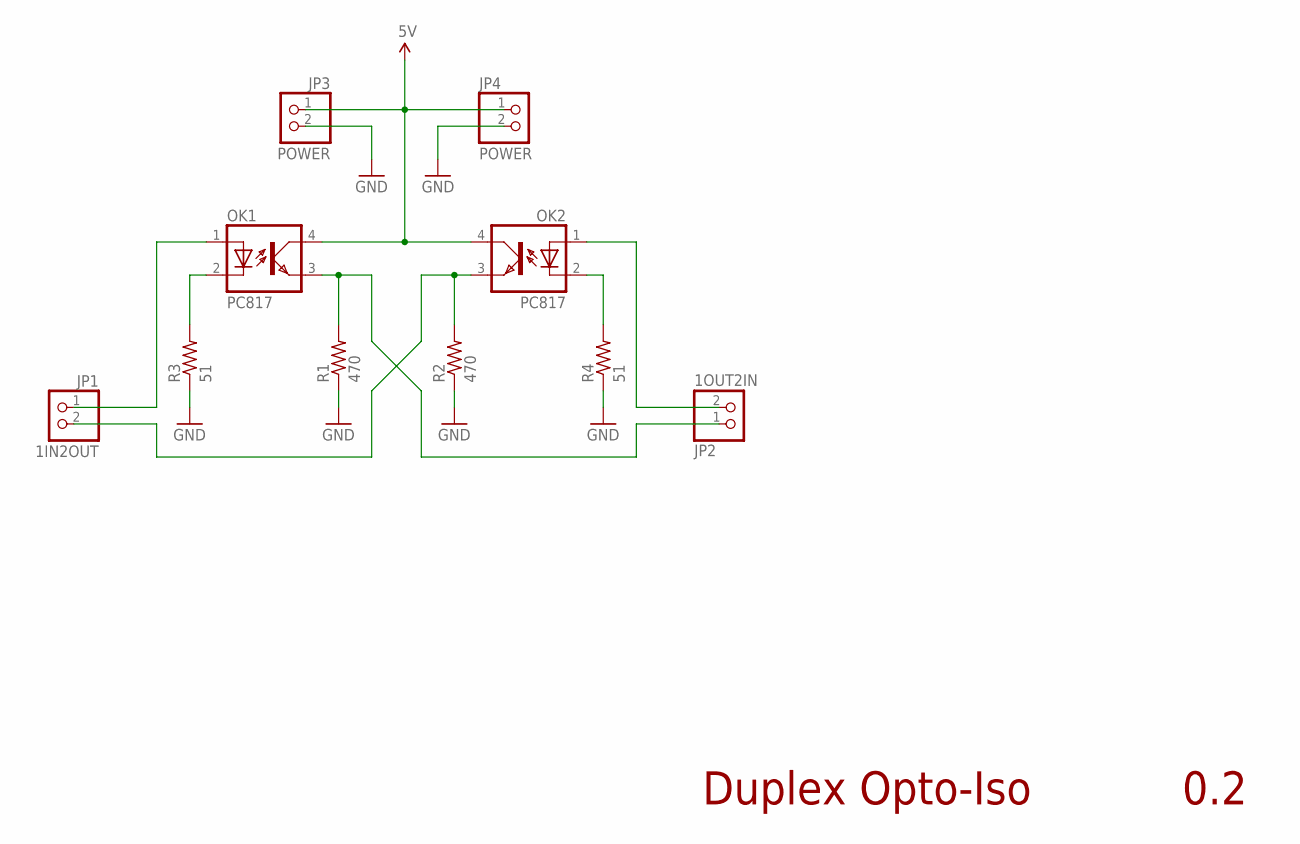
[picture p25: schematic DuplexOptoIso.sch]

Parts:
JP1: 1IN2OUT; 1X02-S
JP2: 1OUT2IN; 1X02-S
JP3, JP4: POWER; 1X02-S
OK1, OK2: PC817; DIL04
R1, R2: 470; 0204/5
R3, R4: 51; 0204/5

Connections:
5V: JP3.1, JP4.1, OK1.4 (COL), OK2.4 (COL)
GND: JP3.2, JP4.2, R1.1, R2.1, R3.1, R4.1
IN1: JP1.1, OK1.1 (A)
IN2: JP2.2, OK2.1 (A)
unnamed: OK1.2 (C), R3.2
unnamed: OK2.2 (C), R4.2
OUT1: JP2.1, OK1.3 (EMIT), R1.2
OUT2: JP1.2, OK2.3 (EMIT), R2.2

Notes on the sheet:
Duplex Opto-Iso
0.2

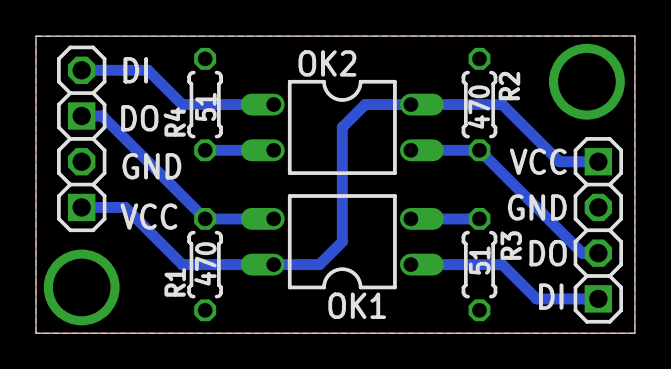
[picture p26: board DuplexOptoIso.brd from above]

Board: 2 copper layers, 33.3 x 16.5 mm, 10 parts (0 on the bottom side), 8 nets.

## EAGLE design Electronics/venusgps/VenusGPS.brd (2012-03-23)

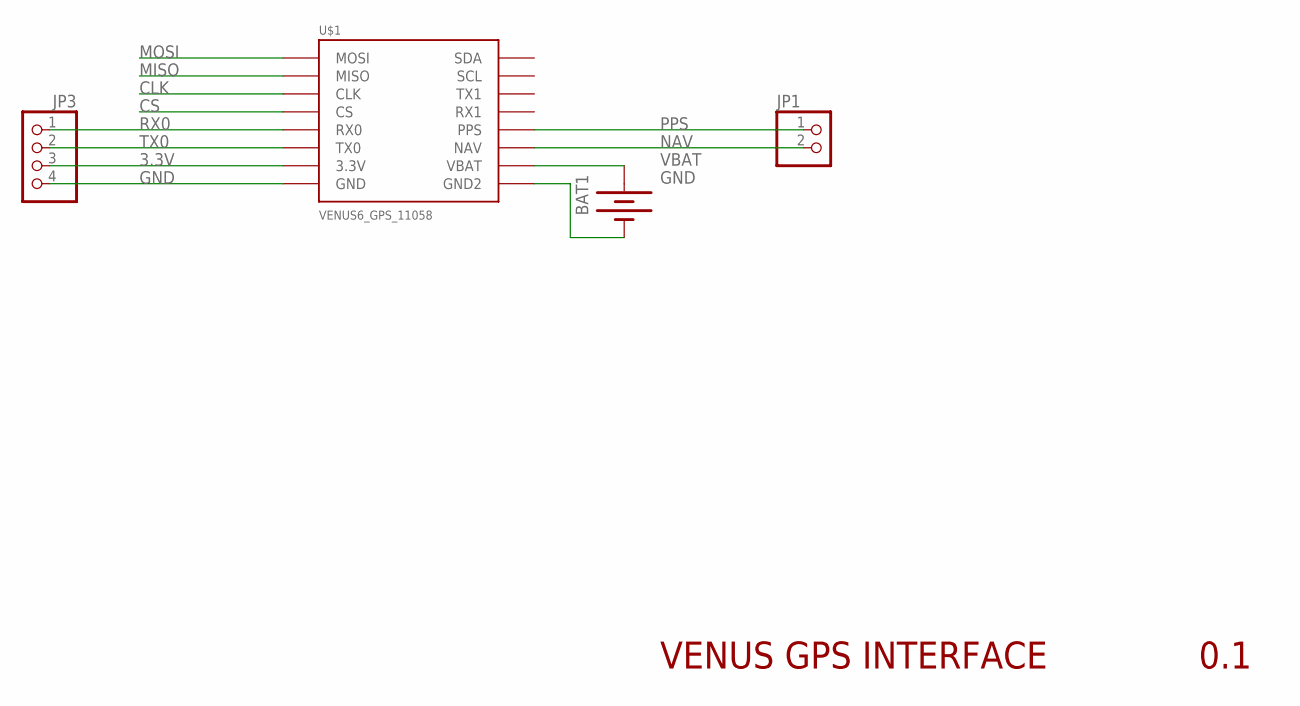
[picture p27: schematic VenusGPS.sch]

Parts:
BAT1: BATTERY12MM; BATTCON_12MM; PARTNO 3000
JP1: PINHD-1X02_2.54; 1X02
JP3: PINHD-1X04_2.54; 1X04
U$1: VENUS6_GPS_11058; VENUS6

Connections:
3.3V: JP3.3, U$1.P7 (3.3V)
CLK: U$1.P3 (CLK)
CS: U$1.P4 (CS)
GND: BAT1.GND (-), JP3.4, U$1.P8 (GND), U$1.P9 (GND2)
MISO: U$1.P2 (MISO)
MOSI: U$1.P1 (MOSI)
NAV: JP1.2, U$1.P11 (NAV)
PPS: JP1.1, U$1.P12 (PPS)
RX0: JP3.1, U$1.P5 (RX0)
TX0: JP3.2, U$1.P6 (TX0)
VBAT: BAT1.PWR@1 (+), U$1.P10 (VBAT)

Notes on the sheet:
VENUS GPS INTERFACE
0.1

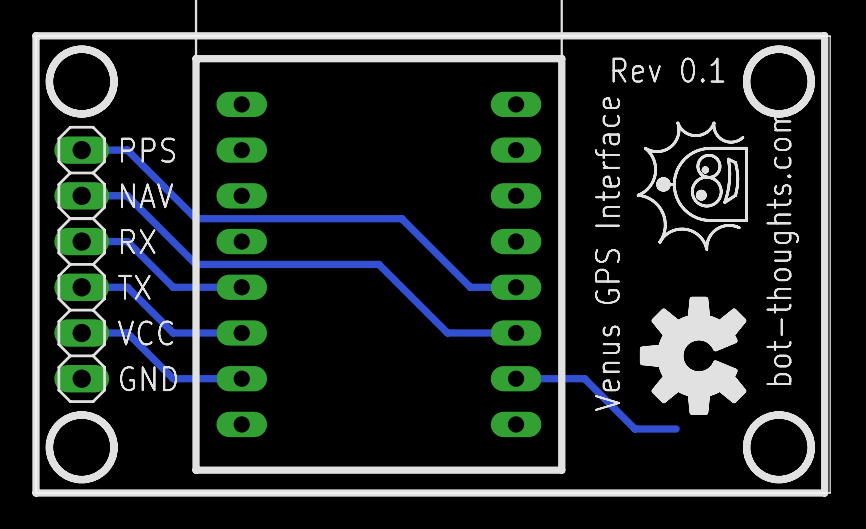
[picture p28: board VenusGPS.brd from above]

Board: 2 copper layers, 44.1 x 25.4 mm, 4 parts (1 on the bottom side), 7 nets.

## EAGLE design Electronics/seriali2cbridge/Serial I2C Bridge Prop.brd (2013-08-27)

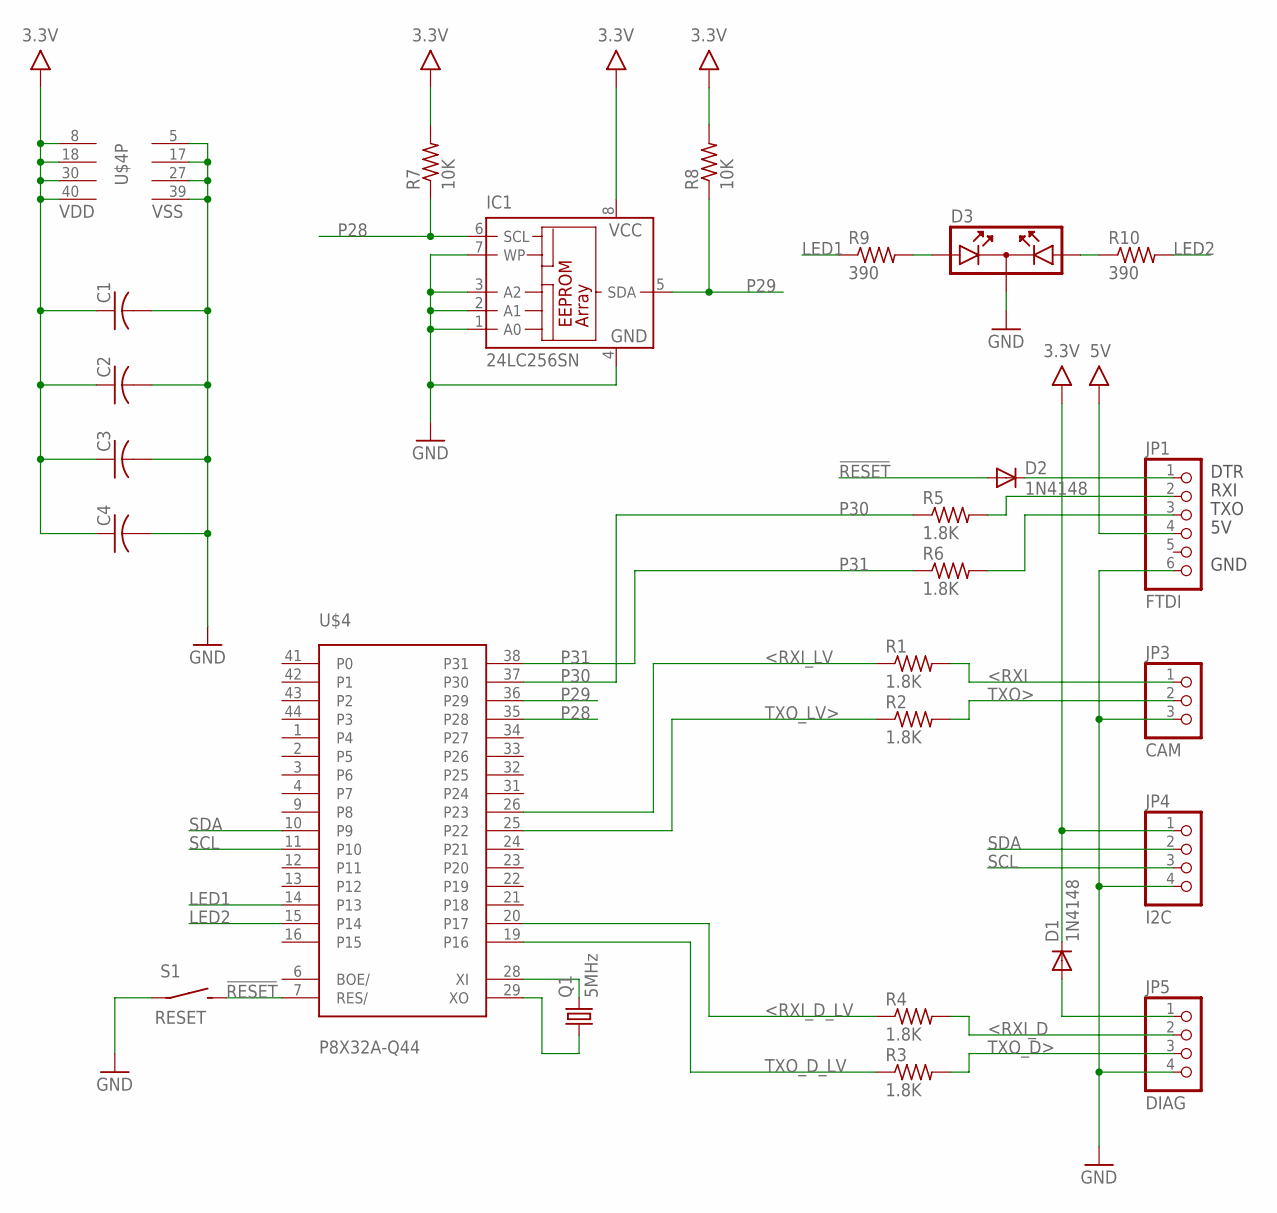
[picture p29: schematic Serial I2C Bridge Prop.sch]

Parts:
C1, C2, C3, C4: C-USC0603; C0603
D1, D2: 1N4148; DO35-7
D3: DUOLED
IC1: 24LC256SN; SO-08
JP1: FTDI; 1X06
JP3: CAM; 1X03
JP4: I2C; 1X04
JP5: DIAG; 1X04
Q1: 5MHz; HC49/S
R1, R2, R3, R4, R5, R6: 1.8K; 0204/5
R7, R8: 10K; 0204/5
R9, R10: 390; 0204/5
S1: RESET; 6MMTACTILE
U$4: P8X32A-Q44

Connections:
3.3V: C1.1, C2.1, C3.1, C4.1, D1.C, IC1.8 (VCC), JP4.1, R7.2, R8.2, U$4.8 (VDD), U$4.18 (VDD), U$4.30 (VDD), U$4.40 (VDD)
5V: JP1.4
!RESET: D2.A, S1.P$2 (S), U$4.7 (RES/)
<RXI: JP3.1, R1.2
<RXI_D: JP5.2, R4.2
<RXI_D_LV: R4.1, U$4.20 (P17)
<RXI_LV: R1.1, U$4.26 (P23)
GND: C1.2, C2.2, C3.2, C4.2, D3.K, IC1.1 (A0), IC1.2 (A1), IC1.3 (A2), IC1.4 (GND), IC1.7 (WP), JP1.6, JP3.3, JP4.4, JP5.4, S1.P$1, U$4.5 (VSS), U$4.17 (VSS), U$4.27 (VSS), U$4.39 (VSS)
LED1: R9.1, U$4.14 (P13)
LED2: R10.2, U$4.15 (P14)
unnamed: D2.C, JP1.1
unnamed: Q1.2, U$4.28 (XI)
unnamed: D1.A, JP5.1
unnamed: Q1.1, U$4.29 (XO)
unnamed: JP1.2, R5.2
unnamed: JP1.3, R6.2
unnamed: D3.A1, R9.2
unnamed: D3.A2, R10.1
P28: IC1.6 (SCL), R7.1, U$4.35 (P28)
P29: IC1.5 (SDA), R8.1, U$4.36 (P29)
P30: R5.1, U$4.37 (P30)
P31: R6.1, U$4.38 (P31)
SCL: JP4.3, U$4.11 (P10)
SDA: JP4.2, U$4.10 (P9)
TXO>: JP3.2, R2.2
TXO_D>: JP5.3, R3.2
TXO_D_LV: R3.1, U$4.19 (P16)
TXO_LV>: R2.1, U$4.25 (P22)

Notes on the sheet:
DTR
RXI
TXO
GND

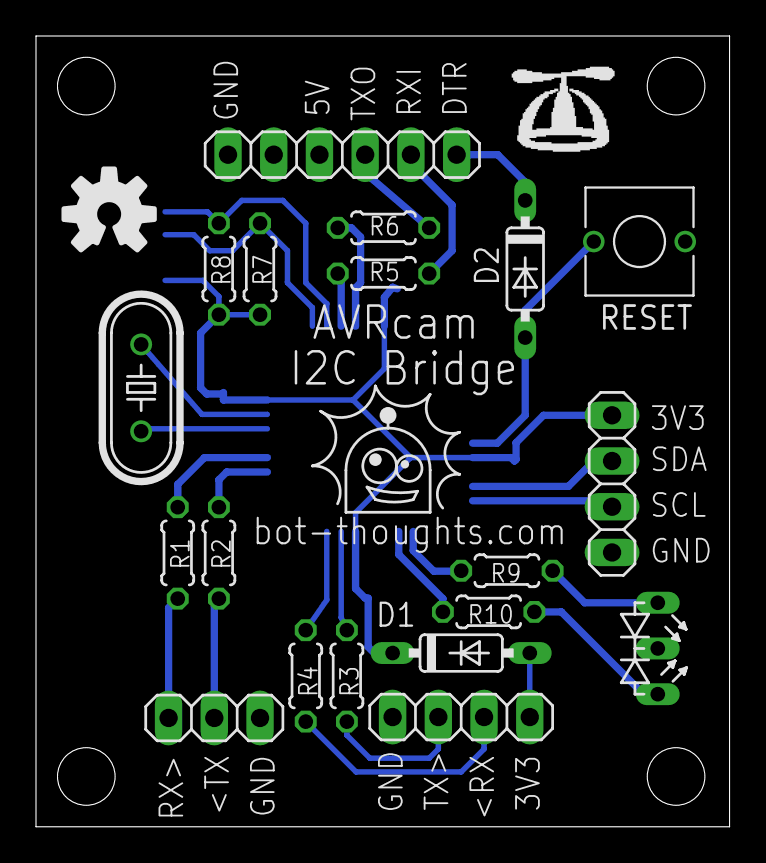
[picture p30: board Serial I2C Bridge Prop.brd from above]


Board: 2 copper layers, 38.5 x 43.9 mm, 25 parts (6 on the bottom side), 27 nets.

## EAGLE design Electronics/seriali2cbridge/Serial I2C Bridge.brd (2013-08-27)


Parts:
C1: 0.1uF; C0805; PARTNO CC0603ZRY5V7BB104
C2, C3, C4: 0.1uF; C0805; PARTNO C1608X5R0J105K
D2: 1N4148; DO35-7
IC1: ATmega328P; DIL28-3; PARTNO DEV-10524
J1: AVRISP; CON6P2R
JP1: I2C; 1X04-S; PARTNO 2211S-04G
JP2: DIAG; 1X04-S; PARTNO 2211S-04G
JP4: FTDI; 1X06-S; PARTNO 2211S-06G
JP5: PWR; 1X02-S
LED1, LED2: STAT1; LED3MM
Q1: 16MHz; CSTLS_G9; PARTNO AWCR-16.00MD
R1: 1K; 0204/5
R2, R5, R7: 330; 0204/5; PARTNO CRCW0603330RJNEA
R4, R6: 1K; 0204/5; PARTNO CRCW0603330RJNEA
S1: RESET\; EVQ11X09; PARTNO SALVAGE

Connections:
3.3V: JP1.1
5V: C3.1, C4.1, D2.C, IC1.7 (VCC), IC1.20 (AVCC), IC1.21 (AREF), J1.2 (VCC), JP4.3, JP5.1, R1.2, R7.1
!RESET: C1.1, C2.1, D2.A, IC1.1 (PC6(/RESET)), J1.5 (!RESET), R1.1, R5.1
<RX: IC1.16 (PB2(SS/OC1B)), JP2.3
<RXD/TXO: IC1.2 (PD0(RXD)), JP4.4
DTR: C1.2, JP4.6
GND: C2.2, C3.2, C4.2, IC1.8 (GND), IC1.22 (GND), J1.6 (GND), JP1.4, JP2.4, JP4.1, JP5.2, LED1.K (C), LED2.K (C), Q1.2 (VSS), S1.1
LV_TX>: JP2.2, R4.2
LV_TXD/RXI>: JP4.5, R6.2
MISO: IC1.18 (PB4(MISO)), J1.1 (MISO)
MOSI: IC1.17 (PB3(MOSI/OC2)), J1.4 (MOSI)
unnamed: IC1.9 (PB6(XTAL1/TOSC1)), Q1.1
unnamed: IC1.10 (PB7(XTAL2/TOSC2)), Q1.3
unnamed: LED1.A, R2.2
unnamed: R5.2, S1.2
unnamed: LED2.A, R7.2
RXI/TXD>: IC1.3 (PD1(TXD)), R6.1
SCK: IC1.19 (PB5(SCK)), J1.3 (SCK), R2.1
SCL: IC1.28 (PC5(ADC5/SCL)), JP1.3
SDA: IC1.27 (PC4(ADC4/SDA)), JP1.2
TX>: IC1.15 (PB1(OC1A)), R4.1

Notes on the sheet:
Serial-I2C Bridge
0.4



Board: 2 copper layers, 45.4 x 44.4 mm, 21 parts (4 on the bottom side), 20 nets.

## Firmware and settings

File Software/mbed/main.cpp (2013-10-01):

/** Code for "Data Bus" UGV entry for Sparkfun AVC 2012
 *  http://www.bot-thoughts.com/
 */

///////////////////////////////////////////////////////////////////////////////////////////////////////
// INCLUDES
///////////////////////////////////////////////////////////////////////////////////////////////////////

#include <stdio.h>
#include <math.h>
#include "mbed.h"
#include "globals.h"
#include "Config.h"
#include "Buttons.h"
#include "Display.h"
#include "Menu.h"
#include "GPSStatus.h"
#include "logging.h"
#include "shell.h"
#include "Sensors.h"
//#include "DCM.h"
//#include "dcm_matrix.h"
#include "kalman.h"
#include "Venus638flpx.h"
#include "Ublox6.h"
#include "Camera.h"
#include "PinDetect.h"
#include "Actuators.h"
#include "IncrementalEncoder.h"
#include "Steering.h"
#include "Schedule.h"
#include "GeoPosition.h"
#include "Mapping.h"
#include "SimpleFilter.h"
#include "Beep.h"
#include "util.h"
#include "MAVlink/include/mavlink_bridge.h"
#include "updater.h"

///////////////////////////////////////////////////////////////////////////////////////////////////////
// DEFINES
///////////////////////////////////////////////////////////////////////////////////////////////////////

#define absf(x) (x *= (x < 0.0) ? -1 : 1)

#define GPS_MIN_SPEED   2.0             // speed below which we won't trust GPS course
#define GPS_MAX_HDOP    2.0             // HDOP above which we won't trust GPS course/position

// Driver configuration parameters
#define SONARLEFT_CHAN   0
#define SONARRIGHT_CHAN  1
#define IRLEFT_CHAN      2
#define IRRIGHT_CHAN     3  
#define TEMP_CHAN        4
#define GYRO_CHAN        5

// Chassis specific parameters
#define WHEEL_CIRC 0.321537             // m; calibrated with 4 12.236m runs. Measured 13.125" or 0.333375m circumference
#define WHEELBASE  0.290
#define TRACK      0.280

#define INSTRUMENT_CHECK    0
#define AHRS_VISUALIZATION  1
#define DISPLAY_PANEL       2

///////////////////////////////////////////////////////////////////////////////////////////////////////
// GLOBAL VARIABLES
///////////////////////////////////////////////////////////////////////////////////////////////////////

// OUTPUT
DigitalOut confStatus(LED1);            // Config file status LED
DigitalOut logStatus(LED2);             // Log file status LED
DigitalOut gpsStatus(LED3);             // GPS fix status LED
DigitalOut ahrsStatus(LED4);            // AHRS status LED
//DigitalOut sonarStart(p18);             // Sends signal to start sonar array pings
Display display;                        // UI display
Beep speaker(p24);                      // Piezo speaker

// INPUT
Menu menu;
Buttons keypad;

// VEHICLE
Steering steerCalc(TRACK, WHEELBASE);   // steering calculator

// COMM
Serial pc(USBTX, USBRX);                // PC usb communications
SerialGraphicLCD lcd(p17, p18, SD_FW);  // Graphic LCD with summoningdark firmware
//Serial *debug = &pc;

// SENSORS
Sensors sensors;                        // Abstraction of sensor drivers
//DCM ahrs;                             // ArduPilot/MatrixPilot AHRS
Serial *dev;                            // For use with bridge

// MISC
FILE *camlog;                           // Camera log

// Configuration
Config config;                          // Persistent configuration
                                        // Course Waypoints
                                        // Sensor Calibration
                                        // etc.

// Timing
Timer timer;                            // For main loop scheduling

// Overall system state (used for logging but also convenient for general use
SystemState state[SSBUF];               // system state for logging, FIFO buffer
unsigned char inState;                  // FIFO items enter in here
unsigned char outState;                 // FIFO items leave out here
bool ssBufOverrun = false;

// GPS Variables
unsigned long age = 0;                  // gps fix age

// schedule for LED warning flasher
Schedule blink;

// Estimation & Navigation Variables
GeoPosition dr_here;                    // Estimated position based on estimated heading
Mapping mapper;

///////////////////////////////////////////////////////////////////////////////////////////////////////
// FUNCTION DEFINITIONS
///////////////////////////////////////////////////////////////////////////////////////////////////////

void initFlasher(void);
void initDR(void);
int autonomousMode(void);
void mavlinkMode(void);
void servoCalibrate(void);
void serialBridge(Serial &gps);
int instrumentCheck(void);
void displayData(int mode);
int compassCalibrate(void);
int compassSwing(void);
int gyroSwing(void);
int setBacklight(void);
int reverseScreen(void);
float gyroRate(unsigned int adc);
float sonarDistance(unsigned int adc);
float irDistance(unsigned int adc);
float getVoltage(void);
extern "C" void mbed_reset();

extern unsigned int matrix_error;

// If we don't close the log file, when we restart, all the written data
// will be lost.  So we have to use a button to force mbed to close the
// file and preserve the data.
//

int dummy(void)
{
    return 0;
}


int resetMe()
{
    mbed_reset();
    
    return 0;
}


int main()
{
    // Let's try setting priorities...
    NVIC_SetPriority(TIMER3_IRQn, 0);	// updater running off Ticker
    NVIC_SetPriority(DMA_IRQn, 1);
    NVIC_SetPriority(EINT0_IRQn, 5);	// wheel encoders
    NVIC_SetPriority(EINT1_IRQn, 5);	// wheel encoders
    NVIC_SetPriority(EINT2_IRQn, 5);	// wheel encoders
    NVIC_SetPriority(EINT3_IRQn, 5);	// wheel encoders
    NVIC_SetPriority(UART1_IRQn, 10);	// GPS p25,p26
    NVIC_SetPriority(I2C0_IRQn, 20);	// sensors?
    NVIC_SetPriority(I2C1_IRQn, 20);	// sensors?
    NVIC_SetPriority(I2C2_IRQn, 20);	// sensors?
    NVIC_SetPriority(UART3_IRQn, 30);	// LCD p17,p18
    NVIC_SetPriority(UART0_IRQn, 30);	// USB
    NVIC_SetPriority(ADC_IRQn, 40);		// Voltage/current
    NVIC_SetPriority(TIMER0_IRQn, 255);	// unused(?)
    NVIC_SetPriority(TIMER1_IRQn, 255);	// unused(?)
    NVIC_SetPriority(TIMER2_IRQn, 255); // unused(?)
    NVIC_SetPriority(SPI_IRQn, 255);	// uSD card, logging


    /*
     * PWM1_IRQn
     * SSP0_IRQn
     * SSP1_IRQn
     * PLL0_IRQn
     * RTC_IRQn
     * BOD_IRQn
     * I2S_IRQn
     * CAN_IRQn
     * ENET_IRQn
     * RIT_IRQn
     * MCPWM_IRQn
     * QEI_IRQn
     * PLL1_IRQn
     * USB_IRQn
     * USBActivity_IRQn
     * CANActivity_IRQn
     */

	// Send data back to the PC
    pc.baud(115200);
    fprintf(stdout, "Data Bus mAGV Control System\n");

    display.init();
    display.status("Data Bus mAGV V3");
   
    fprintf(stdout, "Initialization...\n");
    display.status("Initializing");
    wait(0.2);
    
    // Initialize status LEDs
    ahrsStatus = 0;
    gpsStatus = 0;
    logStatus = 0;
    confStatus = 0;

    //ahrs.G_Dt = UPDATE_PERIOD; 

    fprintf(stdout, "Loading configuration...\n");
    display.status("Load config");
    wait(0.2);
    if (config.load())                          // Load various configurable parameters, e.g., waypoints, declination, etc.
        confStatus = 1;
        
    // Something here is jacking up the I2C stuff
    initSteering();
    initThrottle();
    // initFlasher();                                   // Initialize autonomous mode flasher
        
    sensors.Compass_Calibrate(config.magOffset, config.magScale);
    pc.printf("Declination: %.1f\n", config.declination);
    pc.printf("Speed: escZero=%d escMax=%d top=%.1f turn=%.1f Kp=%.4f Ki=%.4f Kd=%.4f\n", 
        config.escZero, config.escMax, config.topSpeed, config.turnSpeed, 
        config.speedKp, config.speedKi, config.speedKd);
    pc.printf("Steering: steerZero=%0.2f steerGain=%.1f gainAngle=%.1f\n", config.steerZero, config.steerGain, config.steerGainAngle);

    // Convert lat/lon waypoints to cartesian
    mapper.init(config.wptCount, config.wpt);
    for (unsigned int w = 0; w < MAXWPT && w < config.wptCount; w++) {
        mapper.geoToCart(config.wpt[w], &(config.cwpt[w]));
        pc.printf("Waypoint #%d (%.4f, %.4f) lat: %.6f lon: %.6f\n", 
                    w, config.cwpt[w]._x, config.cwpt[w]._y, config.wpt[w].latitude(), config.wpt[w].longitude());
    }

    // TODO: 3 print mag and gyro calibrations

    // TODO 3: remove GPS configuration, all config will be in object itself I think

    display.status("Nav configuration   ");
    steerCalc.setIntercept(config.interceptDist);               // Setup steering calculator based on intercept distance
    pc.printf("Intercept distance: %.1f\n", config.interceptDist);
    pc.printf("Waypoint distance: %.1f\n", config.waypointDist);
    pc.printf("Brake distance: %.1f\n", config.brakeDist);
    pc.printf("Min turn radius: %.3f\n", config.minRadius);

    fprintf(stdout, "Calculating offsets...\n");
    display.status("Offset calculation  ");
    wait(0.2);
    // TODO: 3 Really need to give the gyro more time to settle
    // 5/20 - for some reason it is hanging here
    sensors.gps.disable();
    sensors.Calculate_Offsets();

    fprintf(stdout, "Starting GPS...\n");
    display.status("Start GPS           "); // TODO 3: would be nice not to have to pad at this level
    wait(0.2);
    sensors.gps.setUpdateRate(10);
    sensors.gps.enable();        

    fprintf(stdout, "Starting Scheduler...\n");
    display.status("Start scheduler     ");
    wait(0.2);
    // Startup sensor/AHRS ticker; update every UPDATE_PERIOD
    restartNav();
    startUpdater();

/*
    fprintf(stdout, "Starting Camera...\n");
    display.status("Start Camera        ");
    wait(0.5);
    cam.start();
*/

    // Insert menu system here w/ timeout
    //bool autoBoot=false;

    //speaker.beep(3000.0, 0.2); // non-blocking

    keypad.init();
    
    // Setup LCD Input Menu
    menu.add("Auto mode", &autonomousMode);
    menu.add("Instruments", &instrumentCheck);
    menu.add("Calibrate", &compassCalibrate);
    menu.add("Compass Swing", &compassSwing);
    menu.add("Gyro Calib", &gyroSwing);
    //menu.sdd("Reload Config", &loadConfig);
    menu.add("Backlight", &setBacklight);
    menu.add("Reverse", &reverseScreen);
    menu.add("Reset", &resetMe);
   
    char cmd;
    bool printMenu = true;
    bool printLCDMenu = true;
    
    timer.start();
    timer.reset();

    int thisUpdate = timer.read_ms();    
    int nextUpdate = thisUpdate;
    //int hdgUpdate = nextUpdate;

    while (1) {

        /*
        if (timer.read_ms() > hdgUpdate) {
            fprintf(stdout, "He=%.3f %.5f\n", kfGetX(0), kfGetX(1));
            hdgUpdate = timer.read_ms() + 100;
        }*/

        if ((thisUpdate = timer.read_ms()) > nextUpdate) {
        	// Pull data out of the current state (instate) so we're sure
        	// to get up to date info to display
            SystemState s = state[inState];
            s.gpsHDOP = sensors.gps.hdop();
            s.gpsSats = sensors.gps.sat_count();
            display.update(s);
            nextUpdate = thisUpdate + 2000;
        }
        
        if (keypad.pressed) {
            keypad.pressed = false;
            printLCDMenu = true;
            //causes issue with servo library
            //speaker.beep(3000.0, 0.1); // non-blocking
            switch (keypad.which) {
                case NEXT_BUTTON:
                    menu.next();
                    break;
                case PREV_BUTTON:
                    menu.prev();
                    break;
                case SELECT_BUTTON:
                    display.select(menu.getItemName());
                    menu.select();
                    printMenu = true;
                    break;
                default:
                    printLCDMenu = false;
                    break;
            }//switch  
            keypad.pressed = false;
        }// if (keypad.pressed)

            
        if (printLCDMenu) {
        
            display.menu( menu.getItemName() );
            display.status("Ready.");
            display.redraw();
            printLCDMenu = false;
        }
        
                
        if (printMenu) {
            int i=0;
            fprintf(stdout, "\n==============\nData Bus Menu\n==============\n");
            fprintf(stdout, "%d) Autonomous mode\n", i++);
            fprintf(stdout, "%d) Bridge serial to GPS\n", i++);
            fprintf(stdout, "%d) Calibrate compass\n", i++);
            fprintf(stdout, "%d) Swing compass\n", i++);
            fprintf(stdout, "%d) Gyro calibrate\n", i++);
            fprintf(stdout, "%d) Instrument check\n", i++);
            fprintf(stdout, "%d) Display AHRS\n", i++);
            fprintf(stdout, "%d) Mavlink mode\n", i++);
            fprintf(stdout, "%d) Shell\n", i++);
            fprintf(stdout, "%d) Bridge serial to 2nd GPS\n", i++);
            fprintf(stdout, "R) Reset\n");
            fprintf(stdout, "\nSelect from the above: ");
            fflush(stdout);
            printMenu = false;
        }


        // Basic functional architecture
        // SENSORS -> FILTERS -> AHRS -> POSITION -> NAVIGATION -> CONTROL | INPUT/OUTPUT | LOGGING
        // SENSORS (for now) are polled out of AHRS via interrupt every 10ms
        //
        // no FILTERing in place right now
        // if we filter too heavily we get lag. At 30mph = 14m/s a sensor lag
        // of only 10ms means the estimate is 140cm behind the robot
        //
        // POSITION and NAVIGATION should probably always be running
        // log file can have different entry type per module, to be demultiplexed on the PC
        //
        // Autonomous mode engages CONTROL outputs
        //
        // I/O mode could be one of: MAVlink, serial bridge (gps), sensor check, shell, log to serial
        // Or maybe shell should be the main control for different output modes
        //
        // LOGGING can be turned on or off, probably best to start with it engaged
        // and then disable from user panel or when navigation is ended

        if (pc.readable()) {
            cmd = pc.getc();
            fprintf(stdout, "%c\n", cmd);
            printMenu = true;
            printLCDMenu = true;
            
            switch (cmd) {
                case 'R' :
                    resetMe();
                    break;
                case '0' :
                    display.select(menu.getItemName(0));
                    autonomousMode();
                    break;
                case '1' :
                    display.select("Serial bridge");
                    display.status("Standby.");
                    sensors.gps.enableVerbose();
                    serialBridge( *(sensors.gps.getSerial()) );
                    sensors.gps.disableVerbose();
                    break;
                case '2' :
                    display.select(menu.getItemName(1));
                    compassCalibrate();
                    break;
                case '3' :
                    display.select(menu.getItemName(2));
                    compassSwing();
                    break;
                case '4' :
                    display.select(menu.getItemName(2));
                    gyroSwing();
                    break;
                case '5' :
                    display.select("Instruments");
                    display.status("Standby.");
                    displayData(INSTRUMENT_CHECK);
                    break;
                case '6' :
                    display.select("AHRS Visual'n");
                    display.status("Standby.");
                    displayData(AHRS_VISUALIZATION);
                    break;
                case '7' :
                    display.select("Mavlink mode");
                    display.status("Standby.");
                    mavlinkMode();
                    break;
                case '8' :
                    display.select("Shell");
                    display.status("Standby.");
                    shell();
                    break;
                case '9' :
                    display.select("Serial bridge 2");
                    display.status("Standby.");
                    break;
                default :
                    break;
            } // switch        

        } // if (pc.readable())

    } // while

}



///////////////////////////////////////////////////////////////////////////////////////////////////////
// INITIALIZATION ROUTINES
///////////////////////////////////////////////////////////////////////////////////////////////////////

    
void initFlasher()
{ 
    // Set up flasher schedule; 3 flashes every 80ms
    // for 80ms total, with a 9x80ms period
    blink.max(9);
    blink.scale(80);
    blink.mode(Schedule::repeat);
    blink.set(0, 1);  blink.set(2, 1);  blink.set(4, 1);
}


///////////////////////////////////////////////////////////////////////////////////////////////////////
// OPERATIONAL MODE FUNCTIONS
///////////////////////////////////////////////////////////////////////////////////////////////////////
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

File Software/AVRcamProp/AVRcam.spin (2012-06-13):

CON

  _clkmode = xtal1 + pll16x
  _xinfreq = 5_000_000

  SDA_PIN       = 9 
  SCL_PIN       = 10
  I2CID         = $A0

  RX_PIN        = 17
  TX_PIN        = 16
  BAUD          = 9600

  CAM_RX        = 17
  CAM_TX        = 16
  CAM_BAUD      = 115200

  CHR_TYPE      = 0
  STR_TYPE      = 1
  DEC_TYPE      = 2
  HEX_TYPE      = 3
  BIN_TYPE      = 4

  LED_RED       = 13
  LED_GREEN     = 14

  BUFSIZ        = 128

  BOXMAX        = 8
  BOXSIZ        = 5*BOXMAX        ' 5 bytes per box, 8 boxes 
  COLSIZ        = 48              ' 3 colors (rgb) times 16 values = 48 bytes
  DATSIZ        = BOXSIZ+COLSIZ+1 ' box size = 20 boxes * 6 bytes, color size = 48, plus boxes count

  ERR_FF        = $01
  ERR_PG        = $02
  ERR_SM        = $04
  ERR_ET        = $08
  ERR_TO        = $10

VAR
  long box_sem
  long cog
  long cambuf[BUFSIZ]
  byte response[BUFSIZ]
  long in
  long out

  ' Camera I2C Registers
  byte boxes
  byte box[BOXSIZ]     ' boxes from 0 to BOXSIZ-1
  byte color[COLSIZ]   ' color map from BOXSIZ to BOXSIZ+COLSIZ-1
  byte status
  
  long stack1[BUFSIZ]
  long stack2[BUFSIZ]
  long camstack[BUFSIZ]

OBJ
  pc     : "FullDuplexSerial"
  cam    : "FullDuplexSerial"
  i2c    : "i2cslave"
    
PUB Main
  box_sem := locknew
  cognew(DataHandler, @stack1)
  'cognew(CamRecvHandler, @camstack)
  i2c.Start( SCL_PIN, SDA_PIN, I2CID, @boxes, DATSIZ )

PUB CamRecvHandler | c
  in := out := 0
  repeat
    c := cam.rx
    cambuf[in] := c 
    in := (in+1)&(BUFSIZ-1)
    'fifoStat

PUB DataPrinter | i, j
  ' Print out data storage
  repeat  
    pc.str(String("ColorMap: "))
    repeat i from 0 to COLSIZ
      pc.space
      pc.hex(color[i], 2)
    pc.lf
    pc.str(String("Boxes:    "))
    repeat until not lockset(box_sem)
    pc.dec(boxes)
    pc.lf
    i := 0
    repeat while (i < boxes)
      j := i*5
      pc.space
      pc.dec(box[j]) ' color
      pc.space
      pc.tx("(")
      pc.dec(box[j+1]) ' x1
      pc.tx(",")
      pc.dec(box[j+2]) ' y1
      pc.str(String(") to ("))
      pc.dec(box[j+3]) ' x2
      pc.tx(",")
      pc.dec(box[j+4]) ' y2
      pc.tx(")")
      pc.lf
      i := i + 1
    lockclr(box_sem)
    pc.str(String("Status:   "))
    pc.bin(status, 8)
    pc.lf
    pc.lf
    waitcnt(clkfreq*2+cnt)

PUB DataHandler | i, j, myBoxes, tmp[BOXSIZ], timeout
  status := 0
  cam.start(CAM_RX, CAM_TX, 0, CAM_BAUD)
  pc.start(RX_PIN, TX_PIN, 0, BAUD)
  ' Initialize Color Map
  ' r=144:176, b=32:64, g=16:48
  ' r 0 0 0 0 0 0 0 0 0 128 128 128 0 0 0 0
  ' g 0 0 128 128 128 0 0 0 0 0 0 0 0 0 0 0
  ' b 0 128 128 128 0 0 0 0 0 0 0 0 0 0 0 0
  waitcnt(clkfreq*2+cnt) ' need to wait because stupid i2c routine zeros out the data
  repeat i from 0 to COLSIZ-1
    color[i] := 0
  color[9] := color[10] := color[11] := 128
  color[18] := color[19] := color[20] := 128
  color[33] := color[34] := color[35] := 128

  ' Attempt to initialize camera

  dira[LED_RED] := 1
  dira[LED_GREEN] := 1
  outa[LED_RED] := 1
  outa[LED_GREEN] := 0

  ' Ping camera
  repeat
    waitcnt(clkfreq/4+cnt)
    pc.str(String("Disabling tracking..."))
    outa[LED_RED] := outa[LED_GREEN] := 1
    cam.str(String("DT"))
    cam.cr
    gotAck
    pc.str(String("Pinging camera..."))
    cam.str(String("PG"))
    cam.cr
    if (gotAck == false)
      status |= ERR_PG
      outa[LED_GREEN] := 0
    else
      outa[LED_RED] := 0
      status := 0
      quit

     
  ' send color map
  waitcnt(clkfreq/4+cnt)
  pc.str(String("Sending color map..."))
  outa[LED_RED] := outa[LED_GREEN] := 1
  cam.str(String("SM"))
  repeat i from 0 to COLSIZ-1
    cam.space
    cam.dec(color[i])
    waitcnt(clkfreq/1000+cnt)
  cam.cr
  if (gotAck == false)
    outa[LED_GREEN] := 0
    status |= ERR_SM
  else
    outa[LED_RED] := 0

  ' enable tracking
  waitcnt(clkfreq/4+cnt)
  pc.str(String("Enabling tracking..."))
  outa[LED_GREEN] := outa[LED_GREEN] := 1
  cam.str(String("ET"))
  cam.cr
  if (gotAck == false)
    outa[LED_GREEN] := 0
    status |= ERR_ET
  else
    outa[LED_RED] := 0
  
  pc.lf

  waitcnt(clkfreq/2+cnt)

  outa[LED_RED]   := (status <> 0)
  outa[LED_GREEN] := (status == 0)
     
  ' Start printing out data
  cognew(DataPrinter, @stack2)
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

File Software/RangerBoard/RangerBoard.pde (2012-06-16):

#include <Wire.h>

#define I2C_ADDR 0x11

// ADC variables
#define MAX_ADC 3 // I2C takes up ADC4,5
#define FILT_A 0.2 // exponential filter; gain for current reading
#define FILT_B 0.8 // gain for previous reading
uint16_t adcValue[MAX_ADC];

// UI modes
enum modes { STANDARD, VALUES, MONITOR };
int mode = STANDARD;
char command;
byte data[32];

// Timer
unsigned int tcnt2;

void setup() {
  Serial.begin(9600);
  Wire.begin(I2C_ADDR);
  Wire.onRequest(handleI2CRequest); // register event
  //Wire.onReceive(handleI2CReceive); // register Receive event
  timerSetup();
  delay(1000);
  Serial.println("ADC to I2C Ranger Interface");
  Serial.println("? for help");
  DDRB |= _BV(5); // setup PB5 (Digital 13) as output
}


void loop() {
  if (Serial.available()) {
    char c = Serial.read();
    switch (c) {
      case 'm' :
        mode = MONITOR;
        Serial.println("Monitor mode enabled");
        break;
      case 'q' :
        printValues();
        break;
      case 's' :
      case '?' :
        mode = STANDARD;
        Serial.println("---------------\nm - monitor\nq - query\ns - standard\nv - values\n? - help (this menu)\n---------------\n");
        break;
      case 'v' :
        mode = VALUES;
        break;
      default :
        break;
    }
  }

  if (mode == VALUES) {
    printValues();
  }
  delay(10);
}


void printValues() {
  for (int i=0; i < MAX_ADC; i++) {
    Serial.print(adcValue[i]);
    if (i < (MAX_ADC-1)) Serial.print(",");
  }
  Serial.println();
}



void handleI2CReceive(int numBytes)
{
  char d;
  
  if (mode == MONITOR) 
    Serial.print("I2C Receive: ");

  for (int i=0; i < numBytes; i++) {
    d = Wire.receive(); // pretty much just ignore the command

    if (i == 0) 
      command = d;

    if (i < 32) {
      data[i] = d;
    }

    if (mode == MONITOR) {
      Serial.print(d, HEX);
      Serial.print(" ");
    }
  }
  Serial.println();

  return;
}

/** Function that executes whenever data is requested by master
 *  this function is registered as an event, see setup()
 *
 * Protocol
 * 1) Master requests 4 bytes from us (slave), the bounding box
 * 2) Slave sends sets of 2 bytes for each uint16_t ADC value
 */
void handleI2CRequest()
{
  byte *v = (byte *) adcValue;

  if (mode == MONITOR)
      Serial.print("I2C Request. Sending: ");
  
  for (int i=0; i < 6; i++) {
    data[i] = *v++;
    if (mode == MONITOR) {
      Serial.print(data[i], HEX);
      Serial.print(" ");
    }
  }
  Serial.println();

  Wire.send(data,6);
  
  return;
}

// http://popdevelop.com/2010/04/mastering-timer-interrupts-on-the-arduino/
// author: Sebastian Wallin 
void timerSetup()
{
   /* First disable the timer overflow interrupt while we're configuring */  
  TIMSK2 &= ~(1<<TOIE2);  
  
  /* Configure timer2 in normal mode (pure counting, no PWM etc.) */  
  TCCR2A &= ~((1<<WGM21) | (1<<WGM20));  
  TCCR2B &= ~(1<<WGM22);  
  
  /* Select clock source: internal I/O clock */  
  ASSR &= ~(1<<AS2);  
  
  /* Disable Compare Match A interrupt enable (only want overflow) */  
  TIMSK2 &= ~(1<<OCIE2A);  
  
  /* Now configure the prescaler to CPU clock divided by 128 */  
  TCCR2B |= (1<<CS22)  | (1<<CS20); // Set bits  
  TCCR2B &= ~(1<<CS21);             // Clear bit  
  
  /* We need to calculate a proper value to load the timer counter. 
   * The following loads the value 131 into the Timer 2 counter register 
   * The math behind this is: 
   * (CPU frequency) / (prescaler value) = 125000 Hz = 8us. 
   * (desired period) / 8us = 125.  1000 / 8 = 125
   * MAX(uint8) + 1 - 125 = 131; 
   */  
  /* Save value globally for later reload in ISR */  
  tcnt2 = 131;   
  
  /* Finally load end enable the timer */  
  TCNT2 = tcnt2;  
  TIMSK2 |= (1<<TOIE2);  
}


/* 
 * Install the Interrupt Service Routine (ISR) for Timer2 overflow. 
 * This is normally done by writing the address of the ISR in the 
 * interrupt vector table but conveniently done by using ISR()  */  
ISR(TIMER2_OVF_vect) {  
  /* Reload the timer */  
  TCNT2 = tcnt2;  
  /* toggle pin so that we can confirm our timer */  
  PINB |= _BV(5); // toggle PB5 (Arduino Pin 13)

  for (int i=0; i < MAX_ADC; i++) {
    adcValue[i] = FILT_A*analogRead(i) + FILT_B*adcValue[i]; 
  }
}  

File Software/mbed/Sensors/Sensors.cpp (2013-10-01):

/*

MinIMU-9-Arduino-AHRS
Pololu MinIMU-9 + Arduino AHRS (Attitude and Heading Reference System)

Copyright (c) 2011 Pololu Corporation.
http://www.pololu.com/

MinIMU-9-Arduino-AHRS is based on sf9domahrs by Doug Weibel and Jose Julio:
http://code.google.com/p/sf9domahrs/

sf9domahrs is based on ArduIMU v1.5 by Jordi Munoz and William Premerlani, Jose
Julio and Doug Weibel:
http://code.google.com/p/ardu-imu/

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
*/

#include "Sensors.h"
#include "debug.h"
#include "stdio.h"

#define GYRO_SCALE 14.49787 // TODO: is the sign right here?? yes, see g_sign

#define VFF 50.0 // voltage filter factor

///////////////////// MAGNETOMETER CALIBRATION

Sensors::Sensors():
    //gps(p9, p10),              // Ublox6 GPS
    gps(p26, p25),               // Venus GPS
    _voltage(p19),               // Voltage from sensor board
    _current(p20),               // Current from sensor board
    _left(p30),                  // left wheel encoder
    _right(p29),                 // Right wheel encoder
    _gyro(p28, p27),             // MinIMU-9 gyro
    _compass(p28, p27),          // MinIMU-9 compass/accelerometer
    _rangers(p28, p27),          // Arduino ADC to I2C
    _cam(p28, p27)
{
    for (int i=0; i < 3; i++) {
        m_offset[i] = 0;
        m_scale[i] = 1;
    }

    // TODO: parameterize
    g_scale[0] = 1;
    g_scale[1] = 1;
    g_scale[2] = GYRO_SCALE;

    g_sign[0] = 1;
    g_sign[1] = -1;
    g_sign[2] = -1;

    a_sign[0] = -1;
    a_sign[1] = 1;
    a_sign[2] = 1;

    m_sign[0] = 1;
    m_sign[1] = -1;
    m_sign[2] = -1;

    // upside down mounting
    //g_sign[3] = {1,1,1};        
    //a_sign[3] = {-1,-1,-1};
    //m_sign[3] = {1,1,1}; 
}

/* Compass_Calibrate
 *
 * Set the offset and scale calibration for the compass
 */
void Sensors::Compass_Calibrate(float offset[3], float scale[3])
{
    for (int i=0; i < 3; i++) {
        m_offset[i] = offset[i];
        m_scale[i] = scale[i];
    }    
 
    return;
}


void Sensors::Read_Encoders()
{
    // Odometry            
    leftCount = _left.read();
    rightCount = _right.read();
    leftTotal += leftCount;
    rightTotal += rightCount;
            
    // TODO 3 Sanity check on encoders; if difference between them
    //  is huge, what do we do?  Slipping wheel?  Skidding wheel?
    //  front encoders would be ideal as additional sanity check
    
    // TODO: how do we track distance, should we only check distance everytime we do a nav/pos update?
    // TODO: get rid of state variable
    lrEncDistance  = (WHEEL_CIRC / WHEEL_STRIPES) * (double) leftCount;
    rrEncDistance = (WHEEL_CIRC / WHEEL_STRIPES) * (double) rightCount;
    encDistance = (lrEncDistance + rrEncDistance) / 2.0;
    // compute speed from time between ticks
    int leftTime = _left.readTime();
    int rightTime = _right.readTime();

    // We could also supplement this with distance/time calcs once we get up to a higher
    // speed and encoder quantization error is lower
    // To reduce asymmetry of the encoder operation, we're only reading time
    // between rising ticks. So that means half the wheel stripes

    if (leftTime <= 0) {
        lrEncSpeed = 0;
    } else {
        lrEncSpeed = (2.0 * WHEEL_CIRC / WHEEL_STRIPES) / ((float) leftTime * 1e-6);
    }
    
    if (rightTime <= 0) {
        rrEncSpeed = 0;
    } else {
        rrEncSpeed = (2.0 * WHEEL_CIRC / WHEEL_STRIPES) / ((float) rightTime * 1e-6);
    }
        
    // Dead band
    if (lrEncSpeed < 0.1) lrEncSpeed = 0;
    if (rrEncSpeed < 0.1) rrEncSpeed = 0;
    // TODO: 3 use more sophisticated approach where we count if any ticks have happened lately
    // and if not, reset the speed
    encSpeed = (lrEncSpeed + rrEncSpeed) / 2.0;
}


void Sensors::Read_Gyro()
{
    _gyro.read(g);
    gTemp = (int) _gyro.readTemp();
    
    gyro[_x_] = g_sign[_x_] * (g[_x_] - g_offset[_x_]); // really need to scale this too
    gyro[_y_] = g_sign[_y_] * (g[_y_] - g_offset[_y_]); // really need to scale this too
    gyro[_z_] = (g_sign[_z_] * (g[_z_] - g_offset[_z_])) / g_scale[_z_];

    return;
}

// Reads x,y and z accelerometer registers
void Sensors::Read_Accel()
{
    _compass.readAcc(a);

    accel[_x_] = a_sign[_x_] * (a[_x_] - a_offset[_x_]);
    accel[_y_] = a_sign[_y_] * (a[_y_] - a_offset[_y_]);
    accel[_z_] = a_sign[_z_] * (a[_z_] - a_offset[_z_]);

    return;  
}

void Sensors::Read_Compass()
{
    _compass.readMag(m);
    // TODO: parameterize sign
    // adjust for compass axis offsets and scale
    for (int i=0; i < 3; i++) {
        mag[i] = ((float) m[i] - m_offset[i]) * m_scale[i] * m_sign[i];
    }
    //fprintf(stdout, "m_offset=(%5.5f,%5.5f,%5.5f)\n", ahrs.c_magnetom[0],ahrs.c_magnetom[1],ahrs.c_magnetom[2]);
  
    return;
}

/* doing some crude gryo and accelerometer offset calibration here
 *
 */
void Sensors::Calculate_Offsets()
{
    int samples=128;
    
    for (int i=0; i < 3; i++) {
        g_offset[i] = 0;
        a_offset[i] = 0;
    }

    for(int i=0; i < samples; i++) {  // We take some readings...
        Read_Gyro();
        Read_Accel();
        wait(0.010); // sample at 100hz
        for(int y=0; y < 3; y++) {   // accumulate values
            g_offset[y] += g[y];
            a_offset[y] += a[y];
        }
    }

    for(int y=0; y < 3; y++) {
        g_offset[y] /= samples;
        a_offset[y] /= samples;
    }

    //TODO: if we ever get back to using accelerometer, do something about this.
    //a_offset[_z_] -= GRAVITY * a_sign[_z_]; // I don't get why we're doing this...?
}



void Sensors::Compass_Heading()
{
  /*
  float MAG_X;
  float MAG_Y;
  float cos_roll;
  float sin_roll;
  float cos_pitch;
  float sin_pitch;
  
  // See DCM.cpp Drift_correction()

  // umm... doesn't the dcm already have this info in it?!
  cos_roll = cos(ahrs.roll);
  sin_roll = sin(ahrs.roll);
  cos_pitch = cos(ahrs.pitch);
  sin_pitch = sin(ahrs.pitch);
    
  // Tilt compensated Magnetic filed X:
  MAG_X = mag[_x_] * cos_pitch + mag[_y_] * sin_roll * sin_pitch + mag[_z_] * cos_roll * sin_pitch;
  // Tilt compensated Magnetic filed Y:
  MAG_Y = mag[_y_] * cos_roll - mag[_z_] * sin_roll;
  // Magnetic Heading
  ahrs.MAG_Heading = atan2(-MAG_Y,MAG_X);
  */
}


void Sensors::getRawMag(int rawmag[3])
{
    Read_Compass();
    for (int i=0; i < 3; i++) {
        rawmag[i] = m[i];
    }        
}


// getCurrent is a macro defined above

float Sensors::getVoltage() {
    static float filter = -1.0;
    float v = _voltage * 3.3 * 4.12712;        // 242.3mV/V

    // TODO: median filter to eliminate spikes
    if (filter < 0) {
        filter = v * VFF;
    } else {
        filter += (v - filter/VFF);
    }
    return (filter / VFF);
}
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

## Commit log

2011-02-16 Initial version of all files
    [5V ADC mbed.brd, 5V ADC mbed.sch, Block Diagram.sch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]
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2011-02-17 5V ADC Board: revised logos and routing slightly.
    [5V ADC mbed.brd, 5V ADC mbed.sch]
2011-02-17 Power supply: revised battery terminals, made narrower, moved regulator around. Changed logos.
    [Power Supply.brd, Power Supply.sch]
2011-02-17 Motherboard: Added missing labels, changed OSH logo.
    [Motherboard_simple.brd, Motherboard_simple.sch]
2011-02-17 5V ADC: added OSH logo
    [5V ADC mbed.brd]
2011-03-01 Added new components to reflect recent acquisitions/installations.
    [Master BOM.ods]
2011-03-07 Revised wheel encoder interface board using schmitt trigger and corrected LED circuitry
    [Wheel_Encoder_Adapter_Schmitt.brd, Wheel_Encoder_Adapter_Schmitt.sch]
2011-03-07 Fixed labels on schematic
    [Wheel_Encoder_Adapter_Schmitt.brd, Wheel_Encoder_Adapter_Schmitt.sch]
2011-03-07 Updated silk, minor revisions
    [Wheel_Encoder_Adapter_Schmitt.brd, Wheel_Encoder_Adapter_Schmitt.sch]
2011-03-08 Minor label fixes
    [Wheel_Encoder_Adapter_Schmitt.brd, Wheel_Encoder_Adapter_Schmitt.sch]
2011-03-08 Completely redesigned board
    [Wheel_Encoder_Adapter_3.sch]
2011-03-09 Updated with recent purchases
    [Master BOM.ods]
2011-03-10 Autonomous mode warning strobe flasher
    [WarningFlasher.brd, WarningFlasher.sch]
2011-03-10 Removed LED driver transistor; NE555 can source/sink 225mA (!)
    [WarningFlasher.brd, WarningFlasher.sch]
2011-03-15 Kill Switch board automatically detects tx pulse train and disables MCU control of servo/esc transferring control to radio rx. In other words, to take over control of the robot remotely, turn on the 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
    [RC Kill Switch.brd, RC Kill Switch.sch]
2011-03-16 As built rev 0.1
    [RC Kill Switch.brd, RC Kill Switch.sch]
2011-03-28 5V 1A Power supply with RC truck batt source based on LDO 1117 reg
    [Power Supply 5.brd, Power Supply 5.sch]
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2011-03-28 Added title block, fixed bugs
    [RC Kill Switch.brd, RC Kill Switch.sch]
2011-03-28 Title block fix
    [RC Kill Switch.sch]
2011-03-28 Significant circuit revisions, fixed bug, added indicator LED, added BOM
    [RC Kill Switch.brd, RC Kill Switch.sch]
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2011-10-17 Revised with JST-XH connectors, revised pin/peripheral connections, revised encoder connector, added XBee connector, added analog / serial connector sets, converted to LPCXPresso
    [Motherboard_simple.brd, Motherboard_simple.sch]
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2011-10-17 Updated part no attributes, added docfield / letter border
    [Gfx_LCD.brd, Gfx_LCD.sch]
2011-10-26 Minor fixes, tweaks to BOM, board layout, schematic
    [RC Kill Switch.brd, RC Kill Switch.sch]
2011-10-26 Fixed labeling, revision number
    [RC Kill Switch.sch]
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2011-10-26 fixed revision number
    [Wheel_Encoder_Adapter_Schmitt.sch]
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2012-02-20 Enlarged board for 4 mounting holes, changed encoder pin header orientation
    [Wheel_Encoder_Adapter_Schmitt.brd, Wheel_Encoder_Adapter_Schmitt.sch]
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2012-03-23 Fancy version of motherboard with JST connectors and 2-layer
    [Motherboard.brd, Motherboard.sch]
2012-03-23 Reverting trunk to simple PTH motherboard
    [Motherboard_simple.brd, Motherboard_simple.sch]
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2012-03-23 Reverted to interim branch, shrunk board outline, changed serial pin wiring for consistency, moved button pins, exposed two analog pins, added power selectors for serial ports.
    [Motherboard_simple.brd, Motherboard_simple.sch]
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2012-03-30 Initial Revision for microSD breakout, revised microsd pin header for motherboard, other minor tweaks to motherboard.
    [Motherboard_simple.brd, Motherboard_simple.sch, microSD_Breakout.brd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]
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2012-04-06 Updated to include PI gyro drift correction
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2012-05-14 Completely revised scaling algorithms. Should be much more flexible now and automatically fit everything on the screen.
    [data.csv, waypoints.csv]
2012-05-15 Revised scaling to ensure square plot of points despite aspect ratio of display
    [data.csv]
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2012-05-23 Removed battery, added microSD, more room now, yay.
    [Motherboard_simple.brd, Motherboard_simple.sch]
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2012-06-01 Fixed cam initialization flaws. Fixed race condition with box data.
    [AVRcam.spin]
2012-06-04 Pure pursuit path tracking simulation with steering slop and bias simulated.
    [data.csv, homewpt.csv, waypoints.csv]
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2012-06-13 Updated for new board (Rev 0.1) with different rx/tx pins and with LED indicators. Modified i2c slave bug where it was trouncing on the entire dira register.
    [AVRcam.spin]
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2013-01-17 Major revision for through hole, onboard encoder interface.
    [Motherboard_simple.brd, Motherboard_simple.sch]
2013-01-17 Major revision, added RC takeover switch circuitry. Moved encoder interface.
    [Motherboard_simple.brd, Motherboard_simple.sch]
2013-01-17 Routing tweaks. Added 5V header. Added AVRISP hdr for Tiny
    [Motherboard_simple.brd, Motherboard_simple.sch]
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2013-08-27 Moved RC Mux to subdirectory. Minor changes to various other boards.
    [Motherboard_simple.brd, Motherboard_simple.sch, RC_mux_157.brd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]
2013-09-11 Rev 0.2 as ordered. Widened footprint and changed drill sizes, added labels.
    [RC_MUX.brd, RC_MUX.sch]
2013-10-01 Reworked detect code to simplify and fix behavior bugs, now all runs in timer ISR.
2013-10-01 Consolidated RoverMux electronics and software directories under a single top-level directory
    [RC_MUX.brd, RC_MUX.sch, data.csv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]
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2013-10-02 Updated to fix LED indicator circuits, add AVRISP, moved LEDs, rerouted traces.
    [RC_MUX.brd]
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2013-10-10 Revised schematic changing LED indicator circuit to fix design flaw.
    [RoverMux.sch]
2013-10-11 Created rev 0.5 of motherboard with LPCXpresso, moved to separate directory
    [Motherboard_lpcxpresso.brd, Motherboard_lpcxpresso.sch]
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2013-10-11 Revised schematic after verifying several items. Renamed files.
    [RoverBaseboard.brd, RoverBaseboard.sch]
2013-11-04 Revised power hookup; 3.3V to 3.3V pin, disconnect EXT_POWER from 5V.
    [RoverBaseboard.brd, RoverBaseboard.sch]
2013-11-04 Trying to fix repository
    [RoverBaseboard.brd, RoverBaseboard.sch]
2013-11-04 Fixing repository
    [RoverBaseboard.brd, RoverBaseboard.sch]
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2013-11-05 Bugfix to supply--3.3V regulator now feeds LPCXpresso. Minor tweaks. Powering analog ports more directly. Rerouted power. Moved power pins to align to 0.1" spacing. Heat sink now connected to 3V3 out.
    [RoverBaseboard.brd, RoverBaseboard.sch]
2013-11-22 Change to LDO regulator, added port labels for digital, analog, encoders, change cap values.
    [RoverBaseboard.brd, RoverBaseboard.sch]
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2014-01-29 Revised 8SOIC footprint, replaced 5V regulator and selector with 3.3V regulator to simplify. Moved devices around, simplified routing to pin headers. Placed missing ISP trace. Revised schematic layou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
    [RoverMux.brd, RoverMux.sch]
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2014-01-29 New board for providing 5V power and measuring voltage, amperage.
    [RoverPower.brd, RoverPower.sch]
2014-01-29 Revised traces between bat/esc, added stop mask for tinning. Shrank board size significantly. Added labeling.
    [RoverPower.brd, RoverPower.sch]
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2014-01-29 Fixed Tiny label
    [RoverPower.brd, RoverPower.sch]
2014-02-04 Added ISP pin headers, revised power supply selection layout, added pin header for selecting external 5VIN in addition to selections for 5V or 6V BEC. Renumbered capacitors. Verified cap voltages, et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
    [RoverBaseboard.brd, RoverBaseboard.sch]
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2014-03-11 Revised net names to better reflect encoders. Changed pin header labels to better reflect function.
    [RoverBaseboard.brd, RoverBaseboard.sch]
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2014-05-16 Updated pin names, removed BEC>5V regulator, moved VIN pins back to original spot.
    [RoverBaseboard.brd, RoverBaseboard.sch]
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2015-05-09 moved IR ranger power distr. module to subdir
    [IR Ranger PD Module.brd, IR Ranger PD Module.sch]
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2018-11-28 Added working config file from 2012 with extensive comments.
    [2012_config.txt]

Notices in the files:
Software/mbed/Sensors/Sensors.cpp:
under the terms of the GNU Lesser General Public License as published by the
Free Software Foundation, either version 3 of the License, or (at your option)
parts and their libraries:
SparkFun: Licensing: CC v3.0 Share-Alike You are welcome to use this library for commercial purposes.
